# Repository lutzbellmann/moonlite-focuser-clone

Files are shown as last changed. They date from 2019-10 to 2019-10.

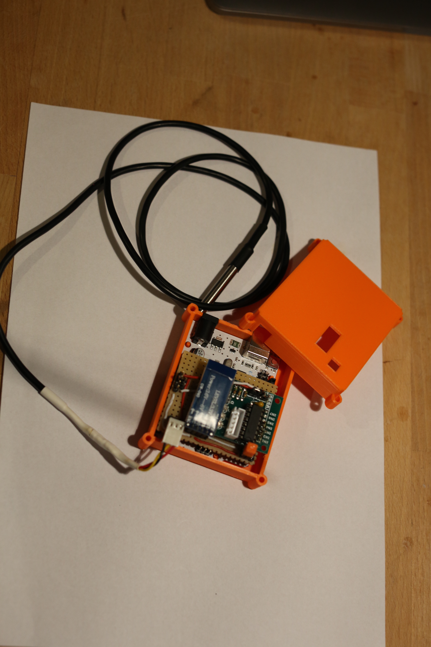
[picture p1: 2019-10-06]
images/FA2A1581.JPG

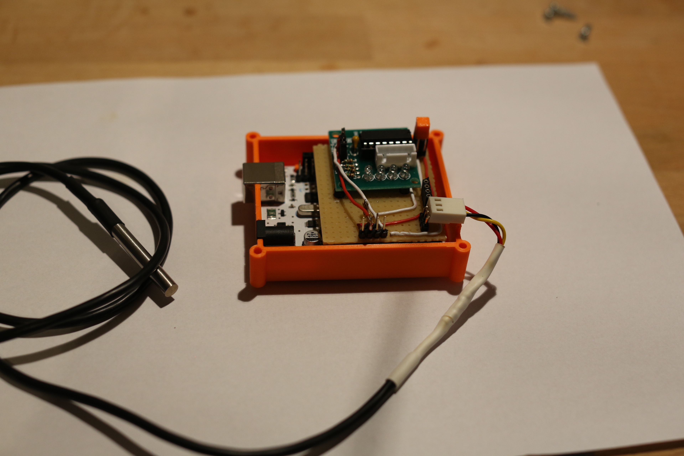
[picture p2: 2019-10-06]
images/FA2A1579.JPG

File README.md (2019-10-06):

# moonlite-focuser-clone
Electric USB or Bluetooth Focuser that is compatible to the Protocol of the popular Moonlite Focuser

# Moonlite-compatible stepper controller
The original code was written by George Carlson in June 2014, so he deserves full credit for this
This is a more feature rich and compatible version, yet some aspects are still missing
 
The version written by Dr. Lutz Bellmann uses the Arduino Uno Rev.3 Board

# Compatibility
The code has been troubleshot against the original and it should be almost compatible to the Moonlite single focuser
Exeptions:
Half Step mode not included
Range is from 0 to 65535 ticks
no backlight supported
this is ment to function remotely and uses serial communication either via bluetooth or USB; if you want to use a DIY handcontroller, you have to extend the code
tested with kstars-bleeding and indilib 

The center concept at 30000 has been skipped, so the full range from 0 to 65535 can be used, yet the default startposition from empty EEPROM is still 30000
Additional features:
Current position, stepping delay(speed), and temperature coefficient are saved to EEPROM and read back after power out
This enables the focuser to remember the last position in the subsequent imaging night.
Temperature acquisition is done by 1-wire T sensor Dallas DS18B20
Temperature can be calibrated by command (not saved to EEPROM, yet)
2-point calibration can be done with Temperature coefficient in (ticks/degreeC) and Compensation can be switched on/off
no delay in movement on temperature readout; conversion commands are executed only in idle condition

# Hardware
The Code has been tested on a Vellemann Arduino Uno Rev3 Board, yet other Atmega based Arduino-like Boards like the Nano or others should work as well
It makes sense that one builds a "shield" for contacting
- the driver board(2PH64011R) for the stepper motor (In1(blue) - Pin4, In2(pink) - Pin5, In3(yellow) - Pin6, In4(orange) - Pin7; +5V to VCC (5V), -Pin to GND
- stepper motor 28BYJ-48
- the Dallas 18B20 digital temperature sensor; use the one with cable and metal casing to stick onto primary mirror or tube; connect to Pin3 as well as VCC (3.3V or 5V) and GND of Arduino
- optional: bluetooth dongle (f.e. HC-06) to be connected to RX and TX as well as VCC(3.3V) and GND of the Arduino; you can't use USB data conenction with Bluetooth dongle connected as well; I made myself a pair of jumpers to be able to disconnect the HC-06
- Case: I will put a couple of STL files and FreeCAD files in the directory to be used as an "application" example; feel free to use or modify as needed

# Installation
The most comfortable way is, to plug your Arduino Board to your PC with USB and use Arduino IDE to "burn" the code to the Board.
Make sure that you have the Libraries
- OneWire
- DallasTemperature
- EEPROM
installed, since they are going to be used by the code.

On connection with USB the Board can be found as a serial device. Any Moonlite compatible software can connect to the board. The Baud Rate is 9600.

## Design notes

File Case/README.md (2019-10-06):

# STL files
- Moonlite_bottom.stl - lower part of the casing
- Moonlite_top.stl - upper part of the casing
- Moonlite_dongle.stl - bluetooth dongle (glue in your jumpers for connecting the bluetooth HC06)
- Moonlite_supp.stl - small support pad (print two) to support the driver board on top a PCB (optional)

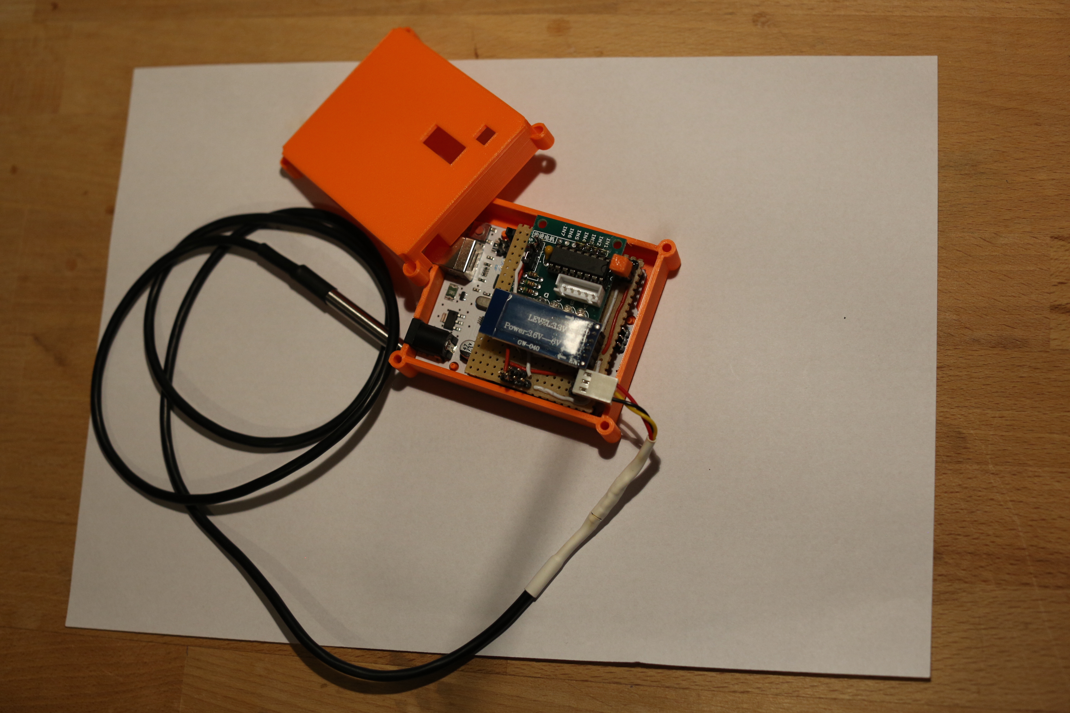
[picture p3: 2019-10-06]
images/FA2A1582.JPG

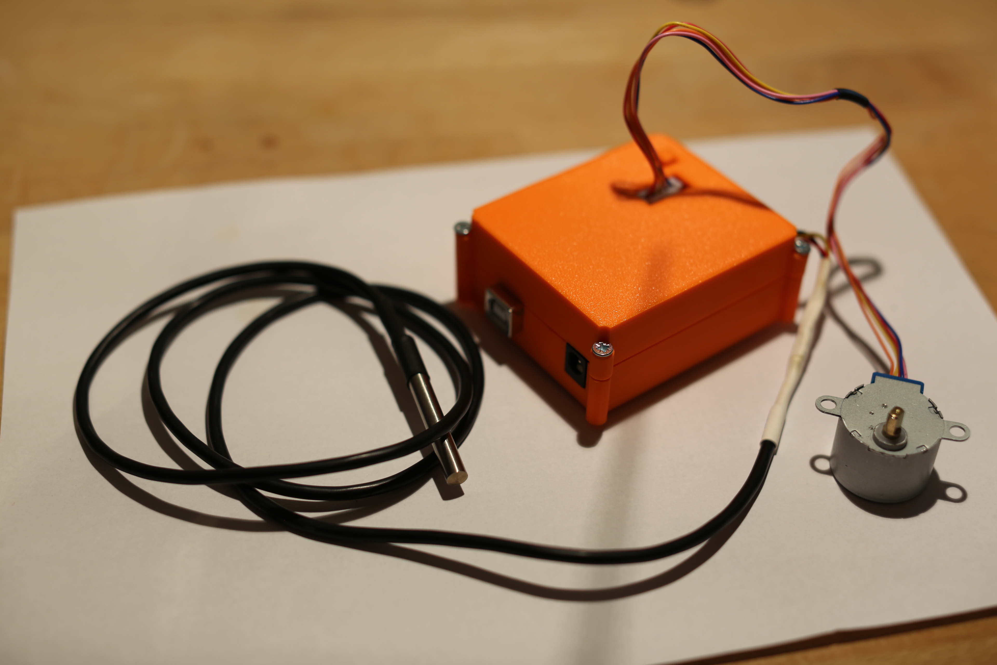
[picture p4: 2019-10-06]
images/FA2A1578.JPG

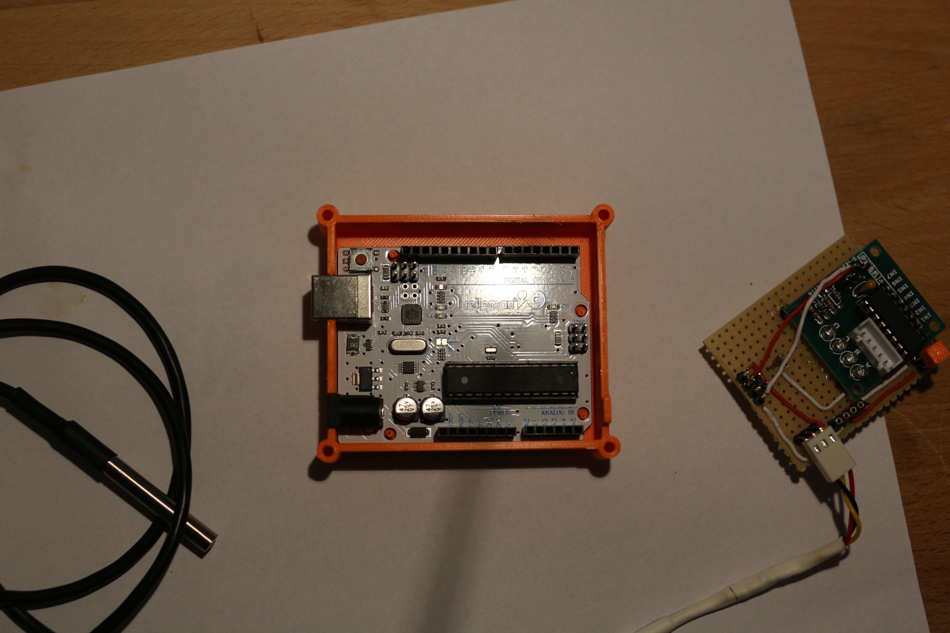
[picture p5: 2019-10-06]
images/FA2A1580.JPG

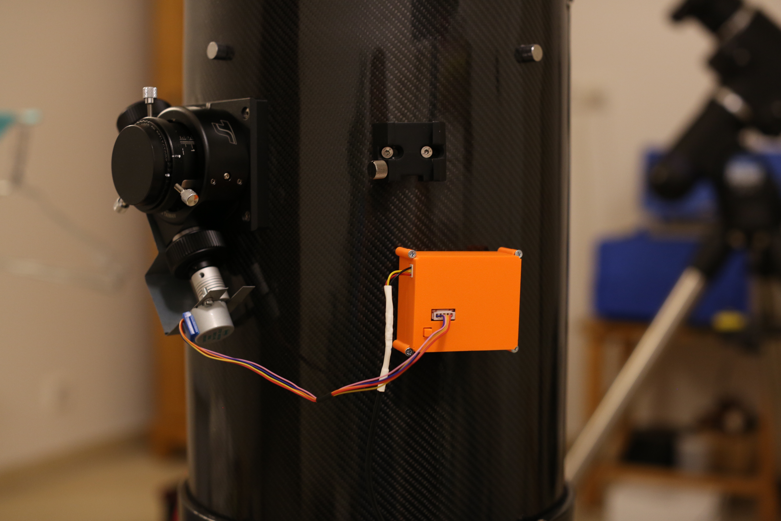
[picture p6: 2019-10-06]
images/FA2A1586.JPG

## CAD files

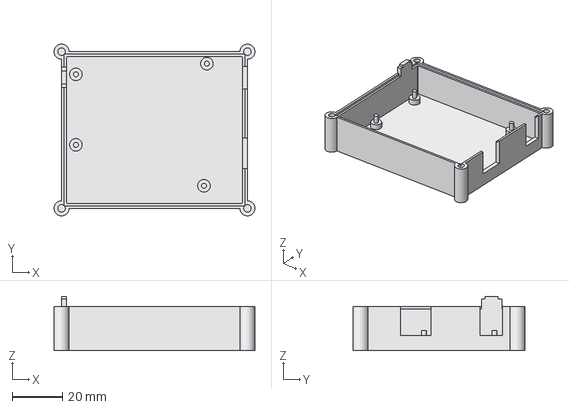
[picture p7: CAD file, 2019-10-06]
Case/Moonlite_bottom.FCStd
79.8 x 68.2 x 21.5 mm

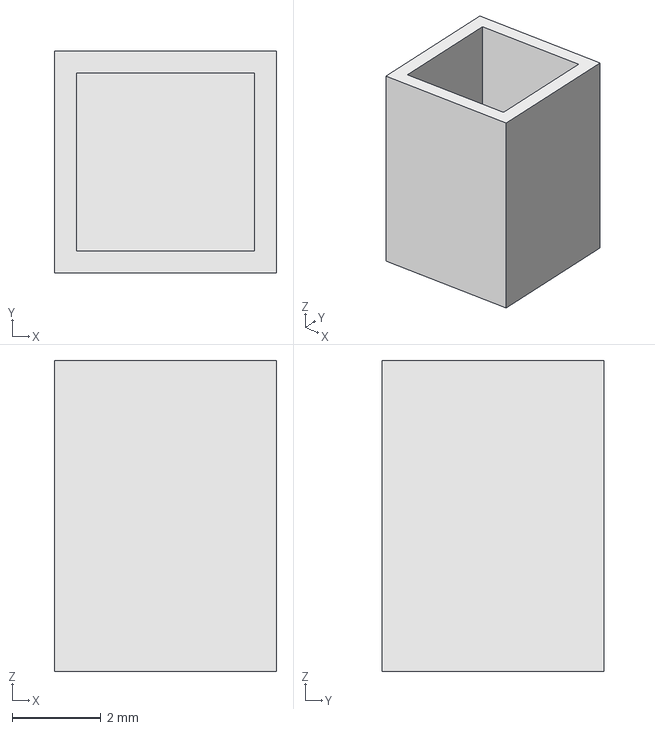
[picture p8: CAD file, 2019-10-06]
Case/Moonlite_dongle.FCStd
5.00 x 5.00 x 7.00 mm

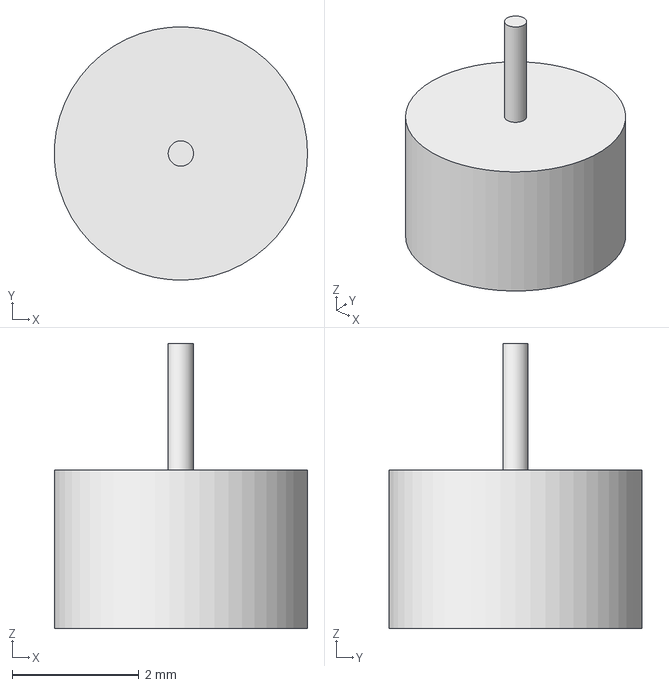
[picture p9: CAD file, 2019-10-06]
Case/Moonlite_supp.FCStd
4.00 x 4.00 x 4.50 mm

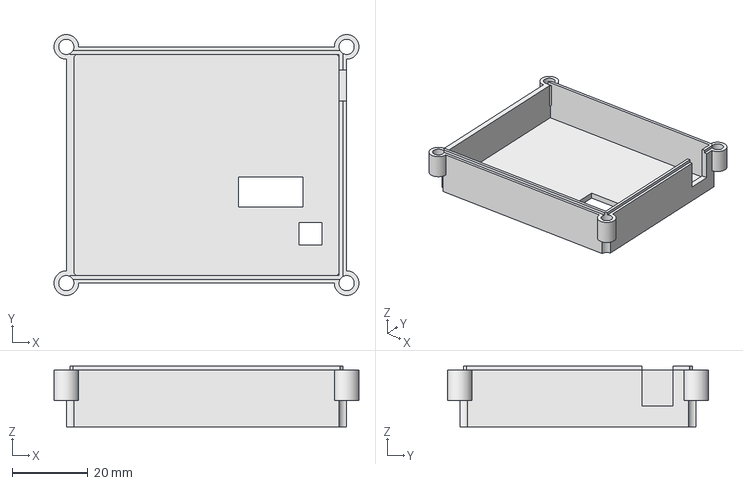
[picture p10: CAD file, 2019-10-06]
Case/Moonlite_top.FCStd
80.3 x 68.7 x 16.0 mm

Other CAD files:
Case/Moonlite_bottom.stl
Case/Moonlite_dongle.stl
Case/Moonlite_supp.stl
Case/Moonlite_top.stl

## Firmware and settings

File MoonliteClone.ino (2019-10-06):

// Moonlite-compatible stepper controller
// The original code was written by George Carlson in June 2014, so he deserves full credit for this
// This is a more feature rich and compatible version, yet some aspects are still missing
// 
// The version written by Dr. Lutz Bellmann uses the Arduino Uno Rev.3 Board
// The code has been troubleshot against the original and it should be almost compatible to the Moonlite single focuser
// Exeptions:
// Half Step mode not included
// Range is from 0 to 65535 ticks
// no backlight supported
// this is ment to function remotely and uses serial communication either via bluetooth or USB; if you want to use a DIY handcontroller, you have to extend the code
// tested with kstars-bleeding and indilib 
//
// The center concept at 30000 has been skipped, so the full range from 0 to 65535 can be used, yet the default startposition from empty EEPROM is still 30000
// Additional features:
// Current position, stepping delay(speed), and temperature coefficient are saved to EEPROM and read back after power out
// This enables the focuser to remember the last position in the subsequent imaging night.
// Temperature acquisition is done by 1-wire T sensor Dallas DS18B20
// Temperature can be calibrated by command (not saved to EEPROM, yet)
// 2-point calibration can be done with Temperature coefficient in (ticks/degreeC) and Compensation can be switched on/off
// no delay in movement on temperature readout; conversion commands are executed only in idle condition


#include <OneWire.h>
#include <DallasTemperature.h>
#include <EEPROM.h>

#define ONE_WIRE_BUS 3  //Sensor DS18B20 am digitalen Pin 3
OneWire oneWire(ONE_WIRE_BUS); //
//Übergabe der OnewWire Referenz zum kommunizieren mit dem Sensor.
DallasTemperature sensors(&oneWire);
int sensorCount;
#define HOME 30000
#define MAXCOMMAND 8
#define SCALE 2 /* Moonlite request Temperature reading *2*/

char offs = 0, coef = 0, inChar, cmd[MAXCOMMAND], param[MAXCOMMAND], line[MAXCOMMAND], tempString[6];
unsigned int hashCmd, Current = HOME, Target = HOME;
long pos;
signed long millisLastMove = 0, DistanceToGo = 0;
bool tempComp = 0, isRunning = 0;
int speed = 2, eoc = 0, idx = 0, minSpeed = 2, maxSpeed = 20, tempTemp;


float wADC, lastTemperature;
int speedTable[16] = {2, 2, 4, 8, 10, 20, 0, 0, 0, 0, 20, 10, 8, 4, 2, 2};
int goTable[16] = { -1, -1, -1, -1, -1, -1, 0, 0, 0, 0, 1, 1, 1, 1, 1, 1};

// Motor connections
int motorPin1 = 7; // Blue - 28BYJ48 pin 1
int motorPin2 = 6; // Pink - 28BYJ48 pin 2
int motorPin3 = 5; // Yellow - 28BYJ48 pin 3
int motorPin4 = 4; // Orange - 28BYJ48 pin 4
// Red - 28BYJ48 pin 5 (VCC)

// lookup table for motor phase control
int StepTable[8] = {0b01001, 0b00001, 0b00011, 0b00010, 0b00110, 0b00100, 0b01100, 0b01000};
int phase = 0;

void forwardstep() {

  Current++;
  if (++phase > 7) phase = 0;
  //stepper1.move(1);
  setOutput(phase);
  for (int i = 0; i < speed >> 1; i++) {
    delay(1);
  }
}

void backwardstep()
{
  Current--;
  if (--phase < 0) phase = 7;

  setOutput(phase);
  for (int i = 0; i < speed >> 1; i++) {
    delay(1);
  }
}

void setOutput(int out)
{
  digitalWrite(motorPin1, bitRead(StepTable[out], 0));
  digitalWrite(motorPin2, bitRead(StepTable[out], 1));
  digitalWrite(motorPin3, bitRead(StepTable[out], 2));
  digitalWrite(motorPin4, bitRead(StepTable[out], 3));
}

float GetTemp(void)
{
  float temperature = 0;
  wADC = sensors.getTempCByIndex(0);
  //Serial.print(wADC);
  temperature = (wADC * SCALE) + offs;
  // The returned temperature is in degrees Celcius * 2 for benefit on MoonLite drivers
  return (temperature);
}

void Tcompensate(void) {
  int newtarget = 0;
  newtarget = Target + ((tempTemp - lastTemperature) * coef)/2;
  Target = newtarget;
  lastTemperature = tempTemp;
}

signed char shexstr2char(char *line) {
  signed char ret = 0;
  ret = strtol(line, NULL, 16);
  return(ret);    
}

long hexstr2long(char *line) {
  long ret = 0;
  ret = strtol(line, NULL, 16);
  return (ret);
}

void clearstate(void)
{
  byte address = 0;
  byte endROM = 0xFF;
  for (address =0; address < endROM; address++)
  {
    EEPROM.write(address, 0xFF);
  }
}

void savestate(void)
{
  byte address = 0;
  byte low, high;
  low = Current&0xFF;
  high = (Current>>8)&0xFF;
  EEPROM.write(address, low);
  address++;
  EEPROM.write(address, high);
  address++;
  EEPROM.write(address, speed);
  address++;
  EEPROM.write(address, coef);
}

void readstate(void)
{
  byte address = 0;
  byte low, high;
  low=EEPROM.read(address);
  address++;
  high=EEPROM.read(address);
  Current = low + ((high << 8)&0xFF00);
  Target = Current;
  if (Current == 0xFFFF){
    Current = HOME;
    Target = HOME;
  }
  address++;
  speed=EEPROM.read(address);
  if (speed == 0xFF)
  {
    speed = 2;
  }
  address++;
  coef = EEPROM.read(address);
  if (coef == 0xFF) {
    coef = 0;
  }
}

//////////////////////////////////////////////////////////////////////////////////////////////////////

// start of program

void setup()

{
  //clearstate(); uncheck to clear EEPROM if you fiddle with the code
  Serial.begin(9600);
  sensors.begin();
  sensors.requestTemperatures(); 
  readstate();
  //setup the motor pins as outputs
  pinMode(motorPin1, OUTPUT);
  pinMode(motorPin2, OUTPUT);
  pinMode(motorPin3, OUTPUT);
  pinMode(motorPin4, OUTPUT);

  //pinMode(RUNLED,OUTPUT); /* yellow LED */
  //pinMode(testPin, OUTPUT);

  memset(line, 0, MAXCOMMAND);
  millisLastMove = millis();

}

// Forever Loop
void loop() {
  
  DistanceToGo = long(Target) - long(Current);
  if (!Serial.available()) {
    // run the stepper if there's no pending command and if there are pending movements

    if (isRunning) {

      if (DistanceToGo > 0)
        forwardstep();

      if (DistanceToGo < 0)
        backwardstep();

      millisLastMove = millis(); /* reset idle timer */
    }

    else { /* Check to see if idle time is up */

      if ((millis() - millisLastMove) > 2000) {
        // if so, turn off motor
        digitalWrite(motorPin1, 0);
        digitalWrite(motorPin2, 0);
        digitalWrite(motorPin3, 0);
        digitalWrite(motorPin4, 0);
        savestate();
      }

      if (tempComp) {
        Tcompensate();
        DistanceToGo = Target - Current;
        isRunning = 1;
      }

    }

    if (DistanceToGo == 0) {
      // if motion is complete
      //digitalWrite(RUNLED,LOW);
      isRunning = 0;
    }

  }

  else {

    // read the command until the terminating # character

    while (Serial.available() && !eoc) {
      inChar = Serial.read();
      if (inChar != '#' && inChar != ':') {
        line[idx++] = inChar;

        if (idx >= MAXCOMMAND)
          idx = MAXCOMMAND - 1;
      }

      else {
        if (inChar == '#')
          eoc = 1;
      }
    }

  } // end if (!Serial.available())



  // process the command we got

  if (eoc) {
    memset(cmd, 0, MAXCOMMAND);
    memset(param, 0, MAXCOMMAND);

    int len = strlen(line);

    if (len >= 1)
      strncpy(cmd, line, 2);

    if (len > 2)
      strncpy(param, line + 2, len - 2);

    memset(line, 0, MAXCOMMAND);
    eoc = 0;
    idx = 0;



    // the stand-alone program sends :C# :GB# on startup

    hashCmd = (byte(cmd[0]) | (byte(cmd[1]) << 8)); /* combine the two command charaters into an unsigned int */
    switch (hashCmd) {
      // GP command Get current position
      case ('P'<<8 | 'G'):
        pos = Current;
        sprintf(tempString, "%04X", pos);
        Serial.print(tempString);
        Serial.print("#");
        break;

      case ('T'<<8 | 'G'):
        // GT command Get Temperature
        if (isRunning == 0)
        {
          tempTemp = GetTemp();          
        }
        sprintf(tempString, "%04X", tempTemp);
        Serial.print(tempString);
        Serial.print("#");
        break;

      case ('I'<<8 | 'G'):
        // GI command 01 if motor running, 00 if not
        if (DistanceToGo != 0)
          Serial.print("01");
        else
          Serial.print("00");
        Serial.print("#");
        break;

      case ('B'<<8 | 'G'):
        // GB command Get current backlight value, always 00
        Serial.print("00#");
        break;

      case ('H'<<8 | 'P'):
        // PH command Find motor home
        Current = HOME;
        isRunning = 1;
        //digitalWrite(RUNLED,HIGH);
        break;
      
      case ('O'<<8 | 'P'):
        // PO command adjust temperature offset
        offs = shexstr2char(param);
        break;
        
      case ('V'<<8 | 'G'):
        // GV command Get software version, always 10
        Serial.print("10#");
        break;

      case ('N'<<8 | 'G'):
        // GN command Get new (target) position
        pos = Target;
        sprintf(tempString, "%04X", pos);
        Serial.print(tempString);
        Serial.print("#");
        break;

      case ('C'<<8 | 'G'):
        // GC command Get temerature coefficient
        sprintf(tempString, "%02X", coef);
        Serial.print(tempString);
        Serial.print("#");
        break;

      case ('C'<<8 | 'S'):
        // SC command Set temperature coefficient
        coef = shexstr2char(param);
        savestate();
        break;
        
      case ('D'<<8 | 'G'):
        // GD command Get motor speed
        sprintf(tempString, "%02X", speed);
        Serial.print(tempString);
        Serial.print("#");
        break;

      case ('D'<<8 | 'S'):
        // SD command Set motor speed
        speed = hexstr2long(param);
        if (speed < minSpeed)
          speed = minSpeed;
        if (speed > maxSpeed)
          speed = maxSpeed;
        savestate();
        break;

      case ('H'<<8 | 'G'):
        // GH command Get half step mode, always 00
        Serial.print("00#");
        break;

      case ('P'<<8 | 'S'):
        // SP command Set current position
        pos = hexstr2long(param);
//        if (pos == 0)
//          pos = HOME;
        Current = pos;
        savestate();
        break;

      case ('N'<<8 | 'S'):
        // SN command Set new position
        pos = hexstr2long(param);
//        if (pos == 0)
//          pos = HOME;
        Target = pos;
        break;

      case ('G'<<8 | 'F'):
        // FG command Start motor command
        isRunning = 1;
        break;

      case ('Q'<<8 | 'F'):
        // FQ command Stop motor command
        isRunning = 0;
        break;
        
      case ('C'):
        // C command Start temperature conversion, only if not moving
        if (isRunning == 0)
        {
          sensors.requestTemperatures();
        }
        break;

      case ('+'):
        // + command sets temperature compensation active
        tempComp = 1;
        tempTemp = GetTemp();
        lastTemperature = tempTemp;
        break;

      case ('-'):
        // - command sets temperature compensation off
        tempComp = 0;
        break;
    }

  } // end process command

} // end forever loop
